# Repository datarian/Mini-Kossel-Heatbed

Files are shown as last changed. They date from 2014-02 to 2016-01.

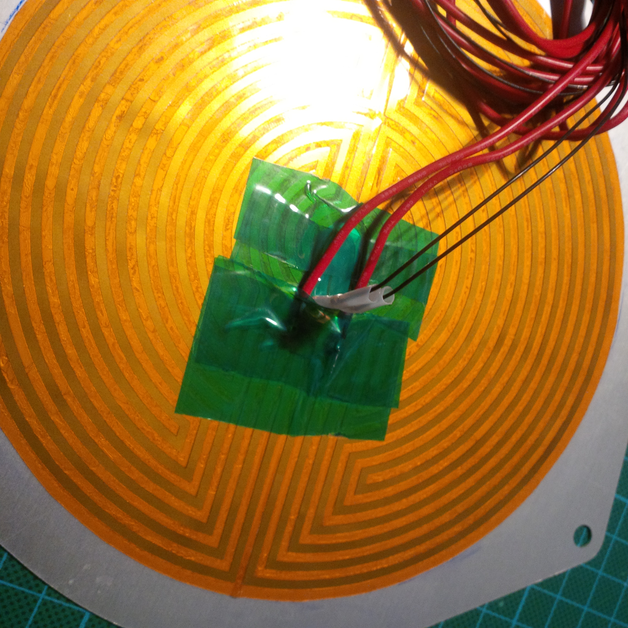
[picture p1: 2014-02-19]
pics/3b_resoldering_complete.jpg

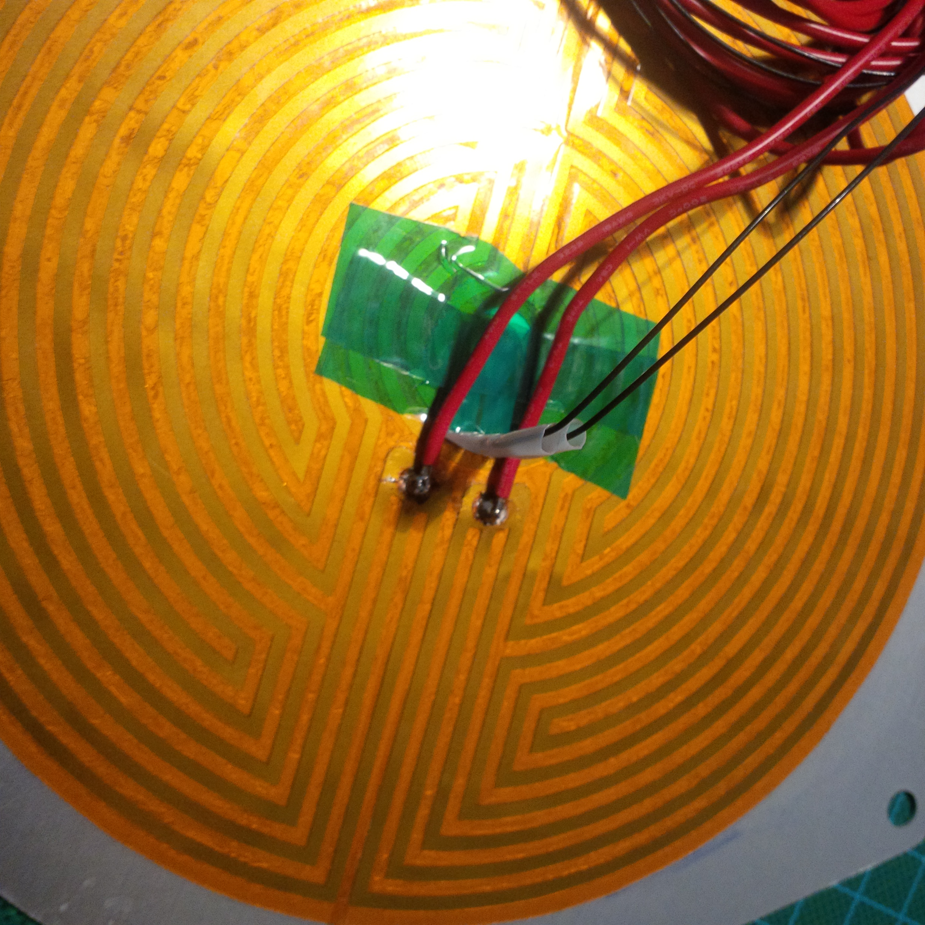
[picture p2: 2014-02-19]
pics/3a_resoldering_job.jpg

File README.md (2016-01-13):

Mini-Kossel-Heatbed
===================

Heatbed design for mini kossels. It is slightly elevated above the base extrusions in order to keep the motors underneath as cool as possible. For the same reason, there's a 3mm cork mat sandwiched between the heater and base aluminum plate.
Quick and dirty steady-state thermal simulations have shown that the bottom alu plate will be about 60°C with a bed heated to 110°C.

Experiences after 18 months or so of operation
-------------------------------------------------
- It works very well in general, heatup times are below 1 minute
- 1 mm aluminum is on the lower end in terms of stiffness. If I redid this, I'd increase the metal to a least 2 mm

Features
--------
- Fits kossel mini
- Solid construction using lasered 1mm aluminum sheets
- thermal isolation towards the frame using ptfe tubing and PE washers for minimized heat loss and faster heatup times.
- Cork isolation under the heater to protect motors underneath
 
Required materials
------------------
- Cut `alu_base`, `alu_fixture`, `alu_ring` from 1 mm aluminum sheet
- cork, circular, diameter around 180mm
- kapton bed heater, 160mm diameter
- 3 pieces of ptfe tubing 6mm od, ideally 3mm id, 6mm long
- 3x M3x20 and nuts to fix the whole thing to your kossel, as well as three compression springs, approx. 6-9mm in height.
- Your choice of build platform, i.e. boro, regular glass, carbon. Diameter 170 mm

Putting it all together
------------------------
Check the exploded view and the pics to get a better idea.

1. Align `alu_fixture` and `alu_ring`, mark the cutout of `alu_ring` on the fixture. It helps to stack `alu_fixture` and `alu_ring` using M6 screws in the holes while doing this.
2. Glue your kapton heater on the marked alu_fixture
3. Resolder the wires on the heater so that they point towards the heater's center. This way they'll go out nicely in the center hole of `alu_base`
4. Prepare cork circle, cut out a hole big enough to get the cables of the heater and thermistor through
5. Prepare the screws and ptfe-tubing (see pics for washer detail), put everything together.
  1. `alu_fixture` with glued-on kapton heater
  2. `alu_ring`
  3. cork circle
  4. `alu_base`
6. Screw setup from top to bottom:
  1. M3 washer
  2. Plastic washer
  3. Into ptfe tube and through heatbed sandwich
  4. Plastic washer
  5. Spring
  6. Plastic washer
  7. Nut in extrusion

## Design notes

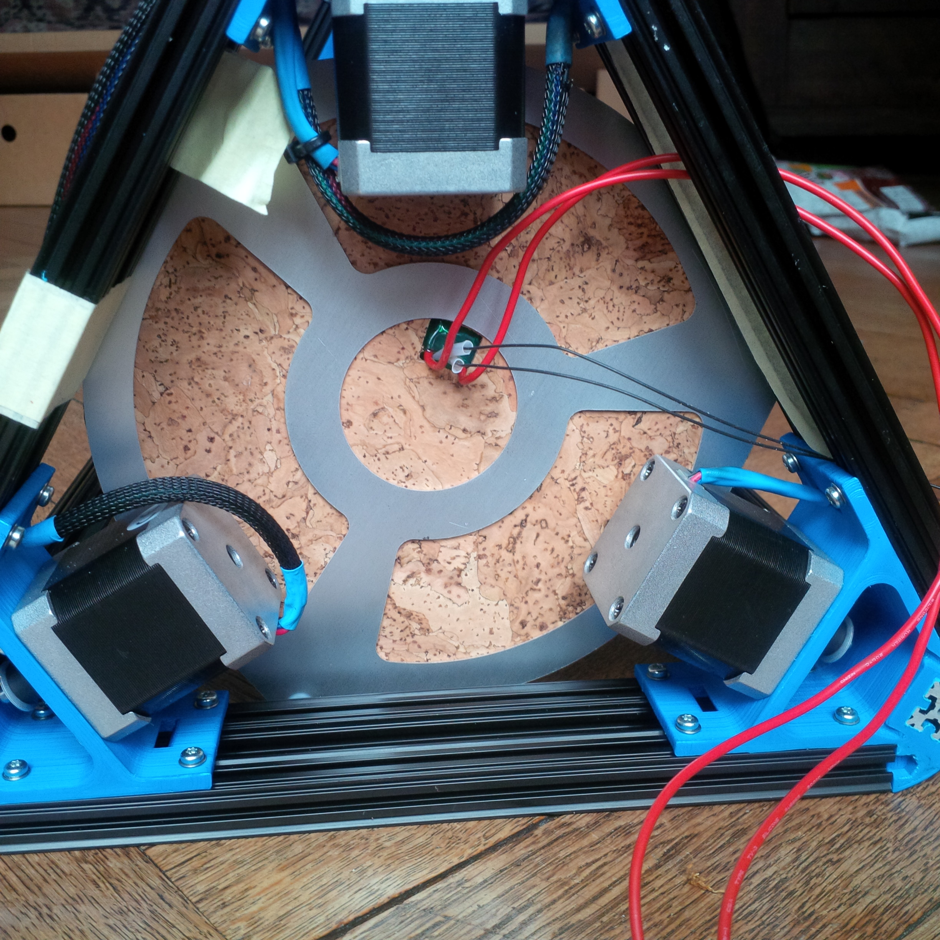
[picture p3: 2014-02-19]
pics/7_view_from_below.jpg

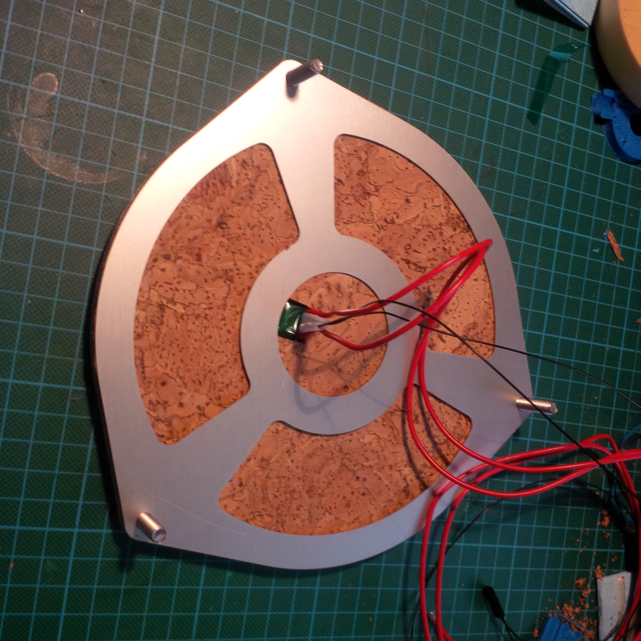
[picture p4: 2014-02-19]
pics/4_leading_wires_out.jpg

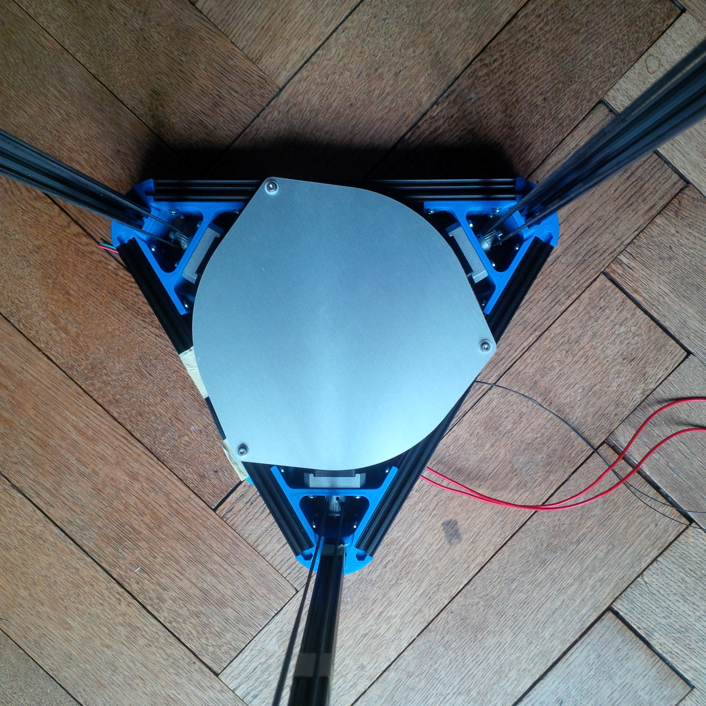
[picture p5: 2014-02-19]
pics/8_view_from_top.jpg

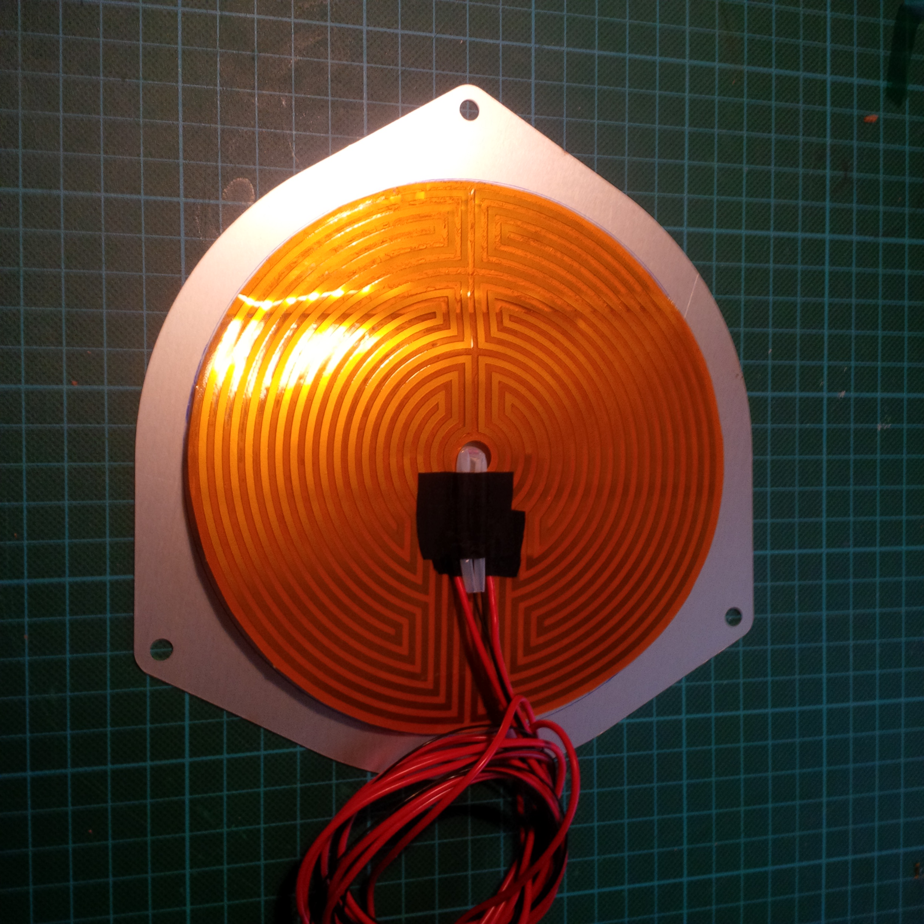
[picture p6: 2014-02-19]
pics/2a_glue_on_heater.jpg

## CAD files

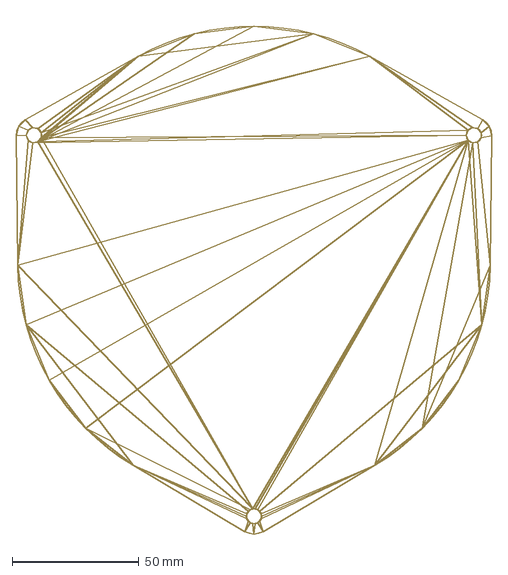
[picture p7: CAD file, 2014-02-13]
alu_fixture.dxf
187.3 x 204.3 mm

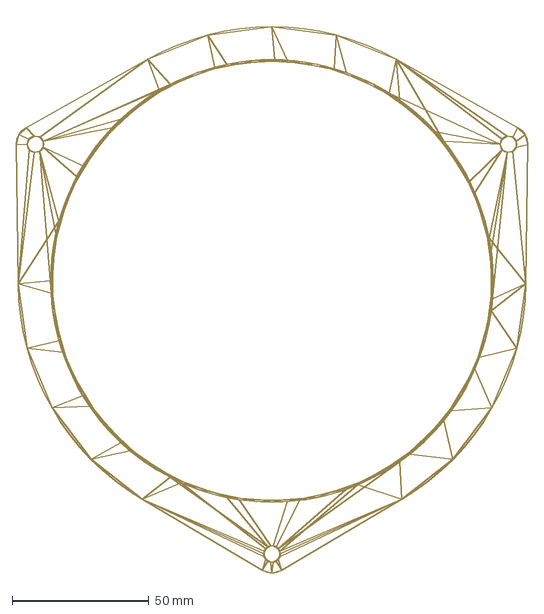
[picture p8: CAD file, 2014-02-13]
alu_ring.dxf
187.3 x 204.3 mm

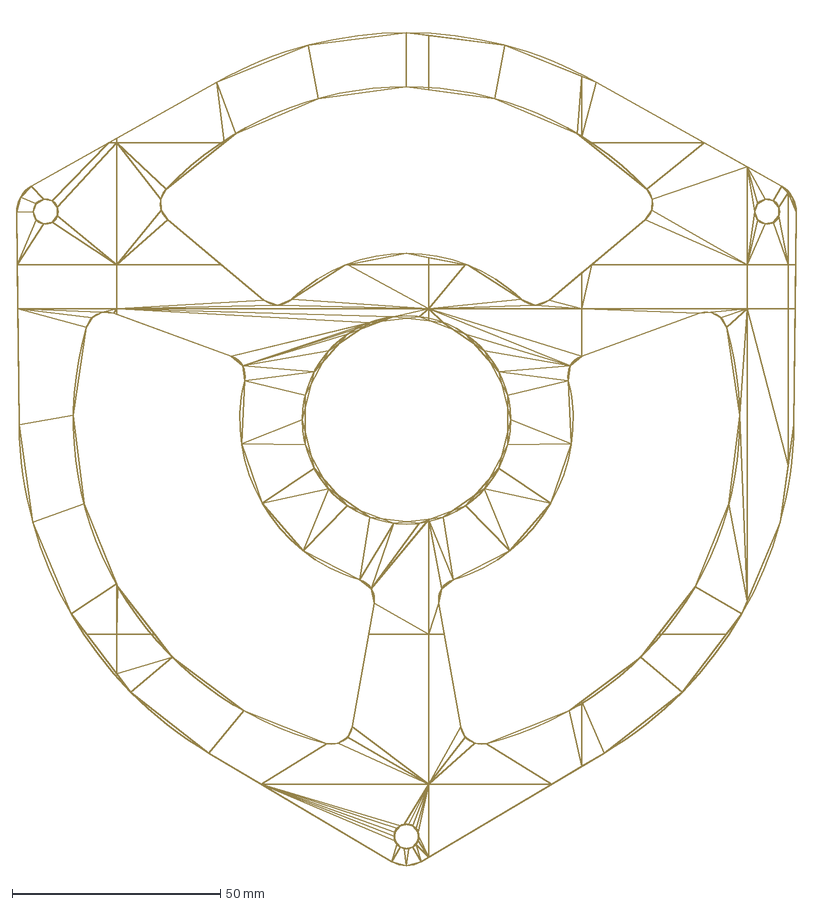
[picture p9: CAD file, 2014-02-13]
alu_base.dxf
187.3 x 204.3 mm

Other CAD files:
alu_base.prt
alu_fixture.prt
alu_ring.prt

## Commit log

2014-02-13 Initial Commit
    Added .prt and .dxf files
    [alu_base.dxf, alu_base.prt, alu_fixture.dxf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]
2014-02-13 Update README.md
    Added features, required materials and setup instructions
